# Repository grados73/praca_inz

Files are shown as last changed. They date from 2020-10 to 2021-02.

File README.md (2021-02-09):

# Praca Dyplomowa (inżynierska)
Tematem pracy była Analiza konstrukcyjna systemu śledzenia linii.
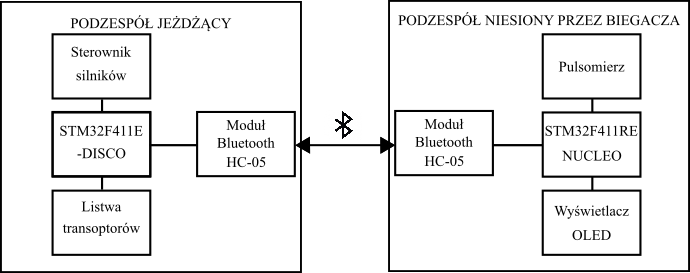
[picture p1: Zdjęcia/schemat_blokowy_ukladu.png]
Block diagram


Zaawansowane rozwiązania techniczne pomagają w osiąganiu coraz to lepszych wyników w różnych dyscyplinach sportowych,
towarzyszą podczas treningów zapewniając wsparcie i umożliwiając pokonywanie kolejnych granic oraz realizację założonych celów.
Wspierają one nie tylko zawodowych sportowców, ale również amatorów, ze względu na ich ogólną dostępność. 
Coraz częściej spotkać można bardzo zaawansowane aplikacje i urządzenia, wykorzystywane w sporcie, 
a oferta firm zajmujących się produkcją takiego sprzętu nieustannie się poszerza o nowe rozwiązania.

Celem pracy była realizacja robota, wykorzystującego system śledzenia linii, w celu utrzymywania zadanego tempa biegacza trenującego na bieżni lekkoatletycznej, 
aby osiągnąć większą efektywność treningów. Projekt składa się z dwóch podzespołów. 
Pierwszy z nich jest niesiony przez biegacza, jego zadaniem jest pomiar tętna i utrzymanie go w zakresie ustalonym przez ćwiczącego. 
Drugi moduł ma za zadanie jechać po ustalonej linii i utrzymywać zadane tempo.

https://youtu.be/Zt6rl9LgnUI

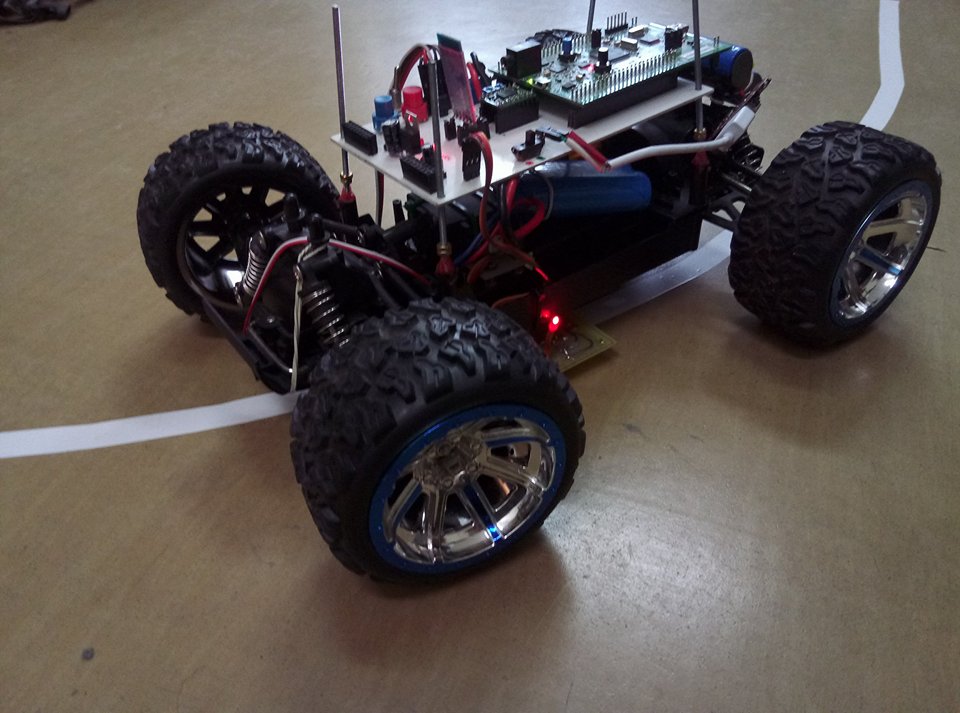
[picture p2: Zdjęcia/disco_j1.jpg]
Decio1

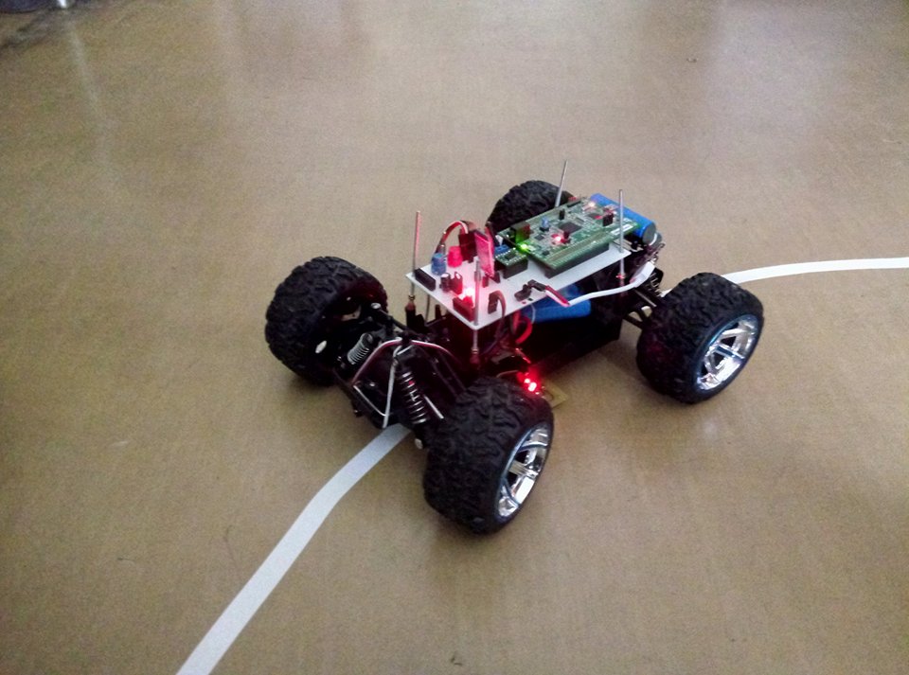
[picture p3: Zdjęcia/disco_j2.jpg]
Decio2

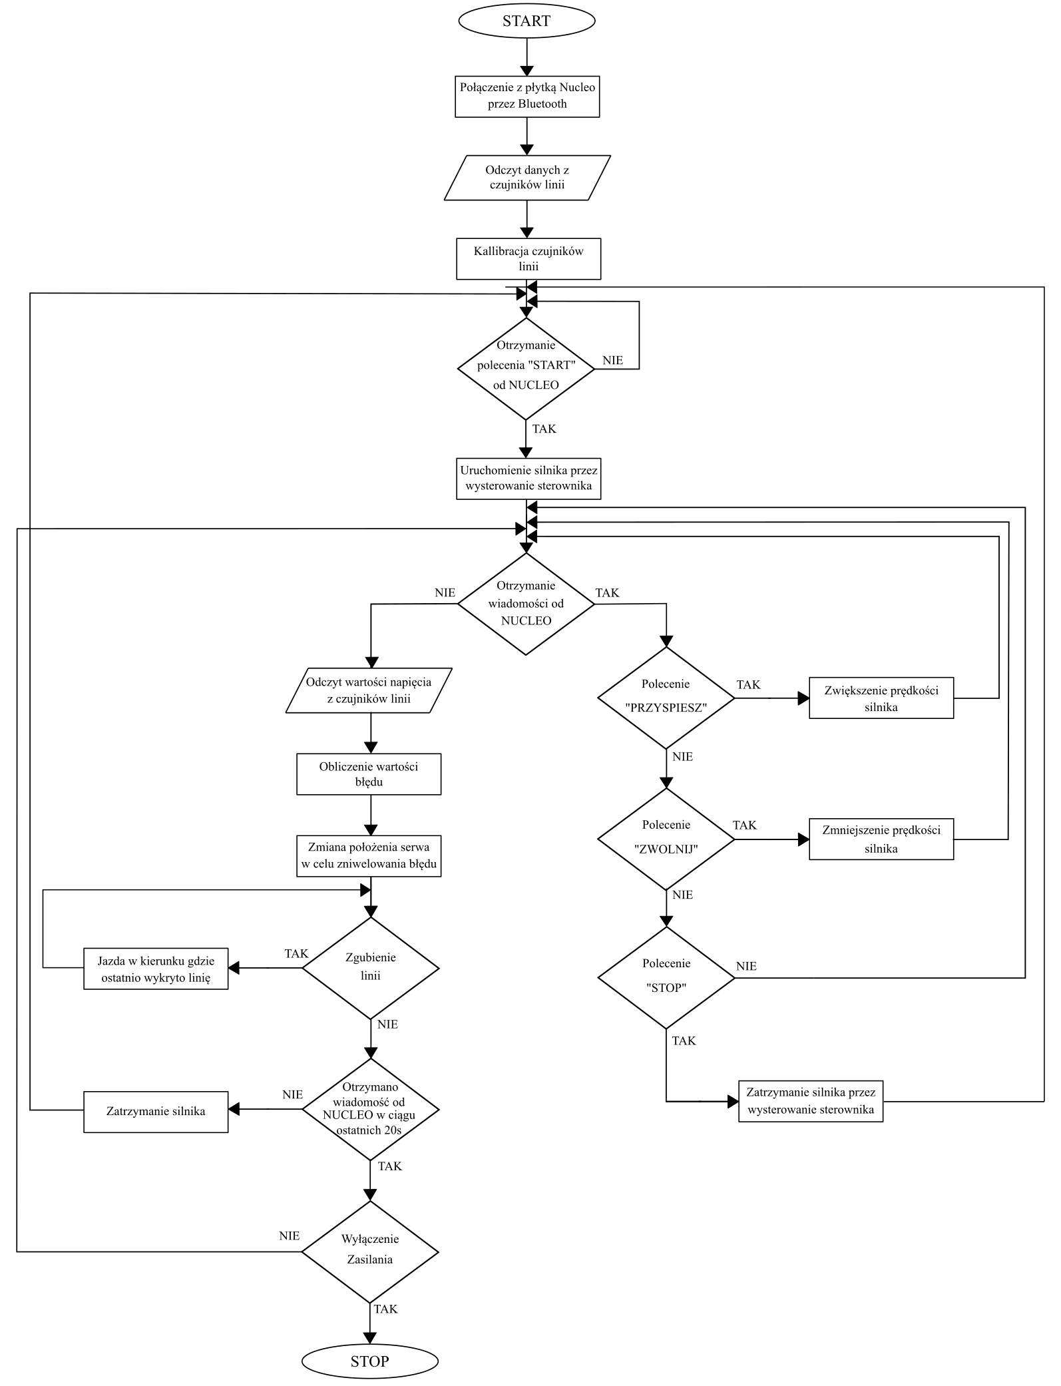
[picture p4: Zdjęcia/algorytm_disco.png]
ALGD1

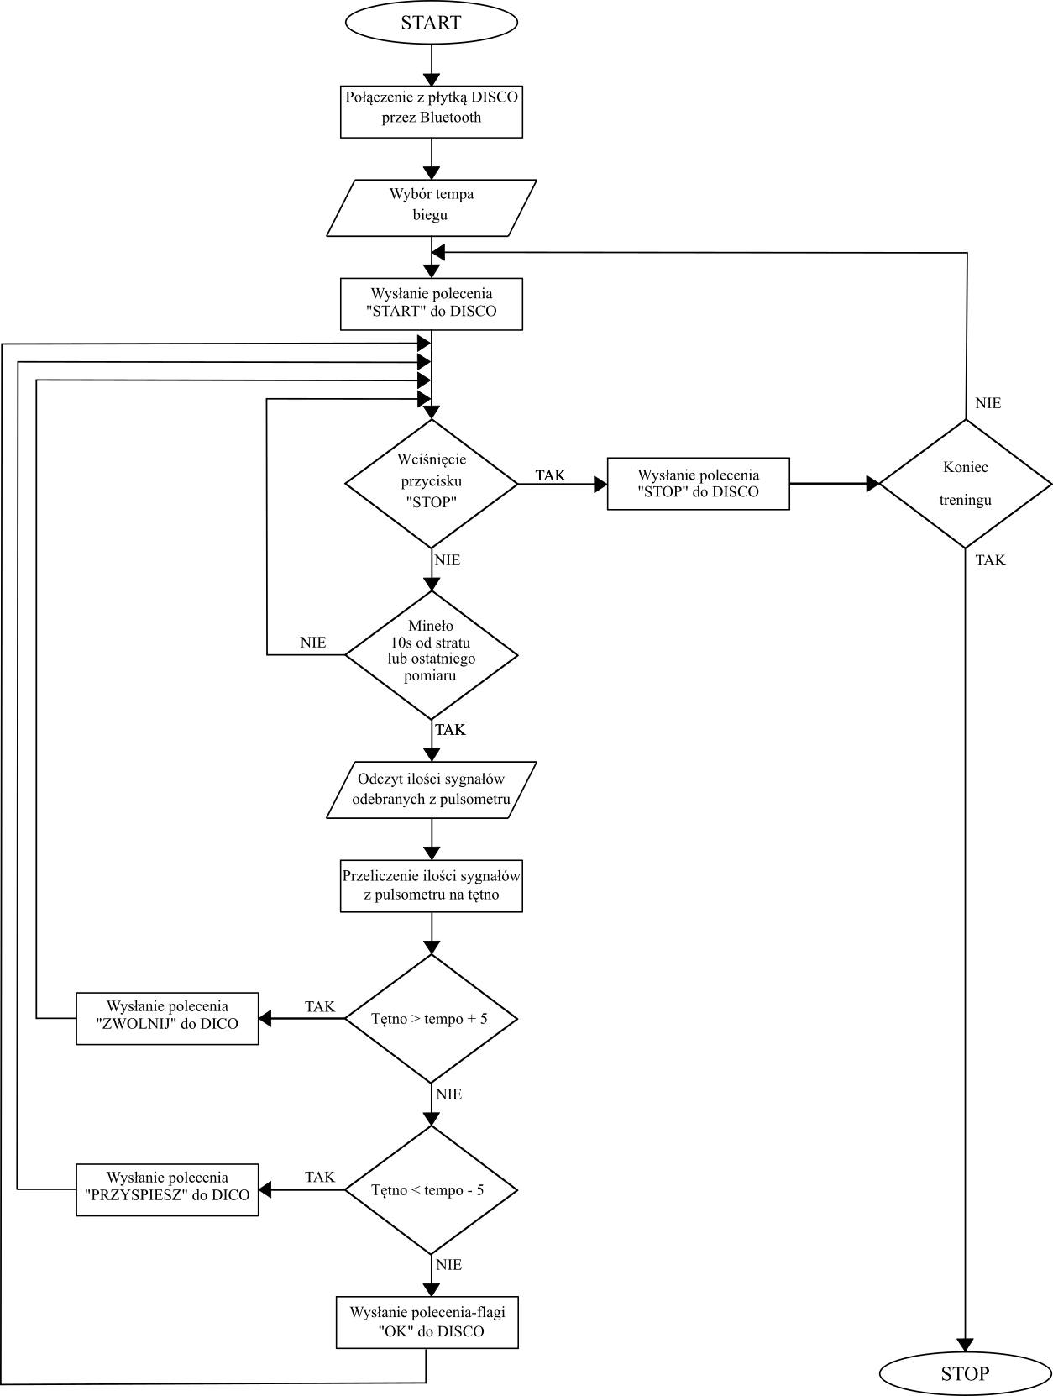
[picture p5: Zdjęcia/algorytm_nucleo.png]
ALGN1


Created by https://www.linkedin.com/in/kamil-gradowski-8706991aa - feel free to contact me! grados73

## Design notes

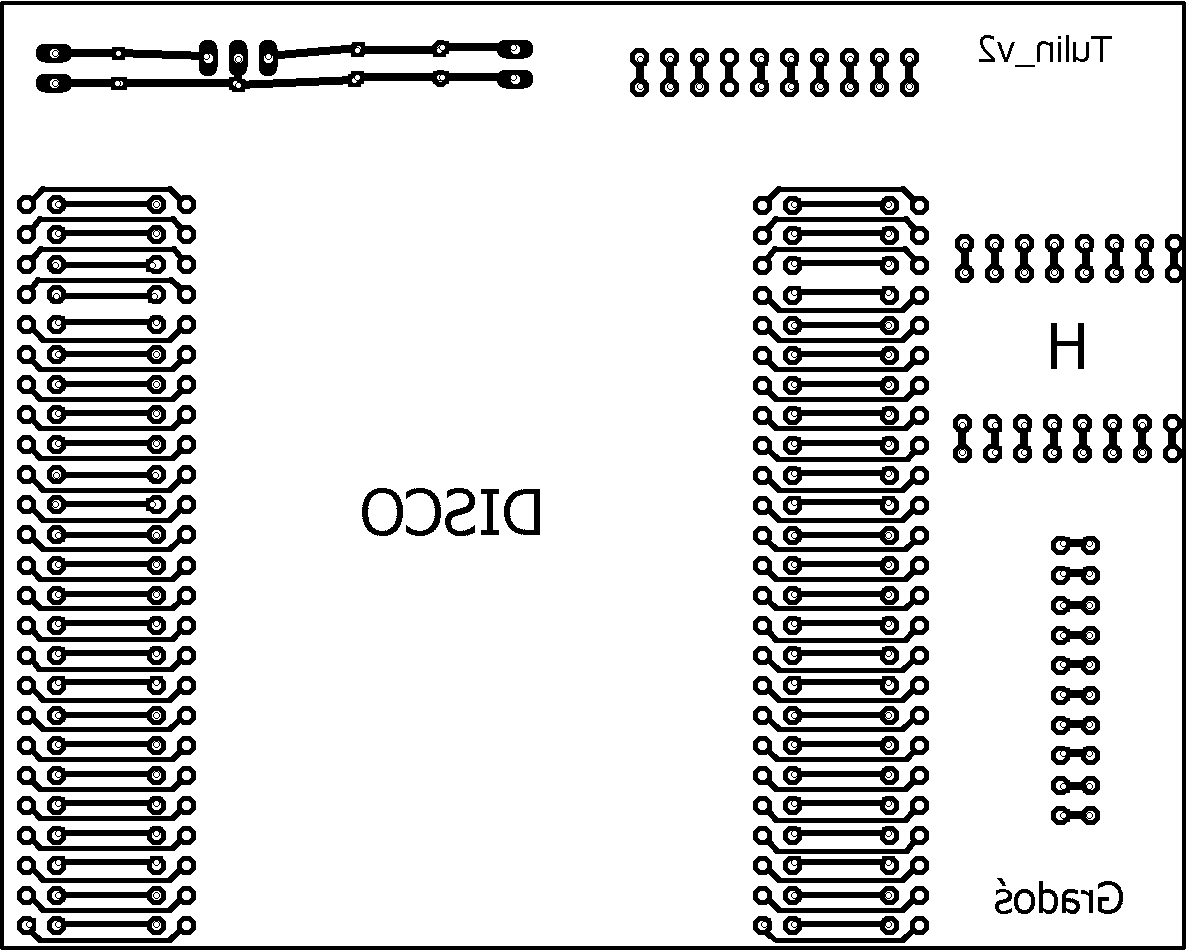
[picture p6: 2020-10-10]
eagle/Tulin_v.2_pr/Jedyna_prawdziwa.png

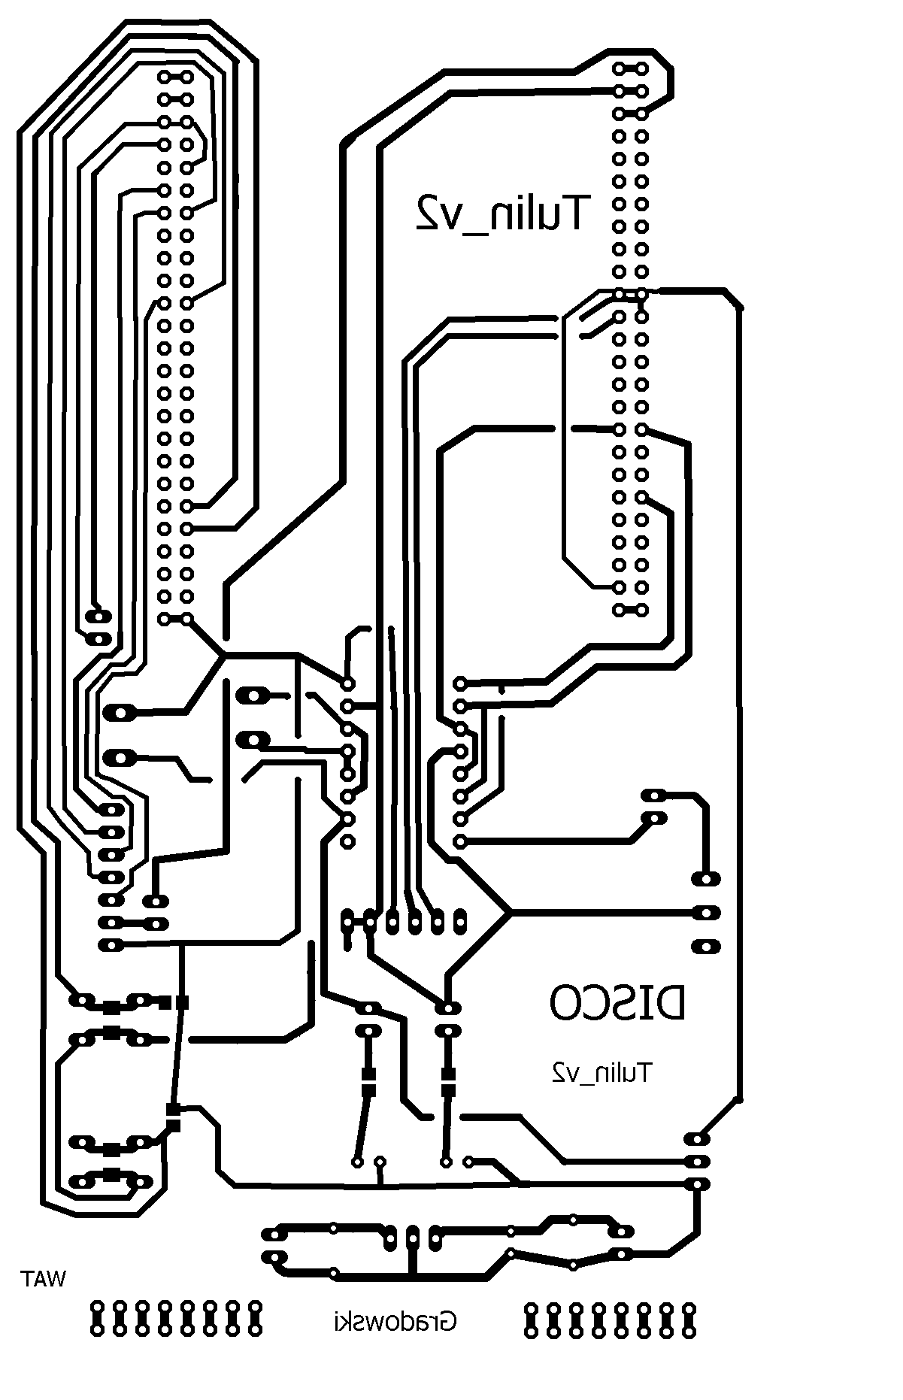
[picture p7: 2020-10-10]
eagle/TULIN_GOTOWE/Tulin_do_spr/got.png

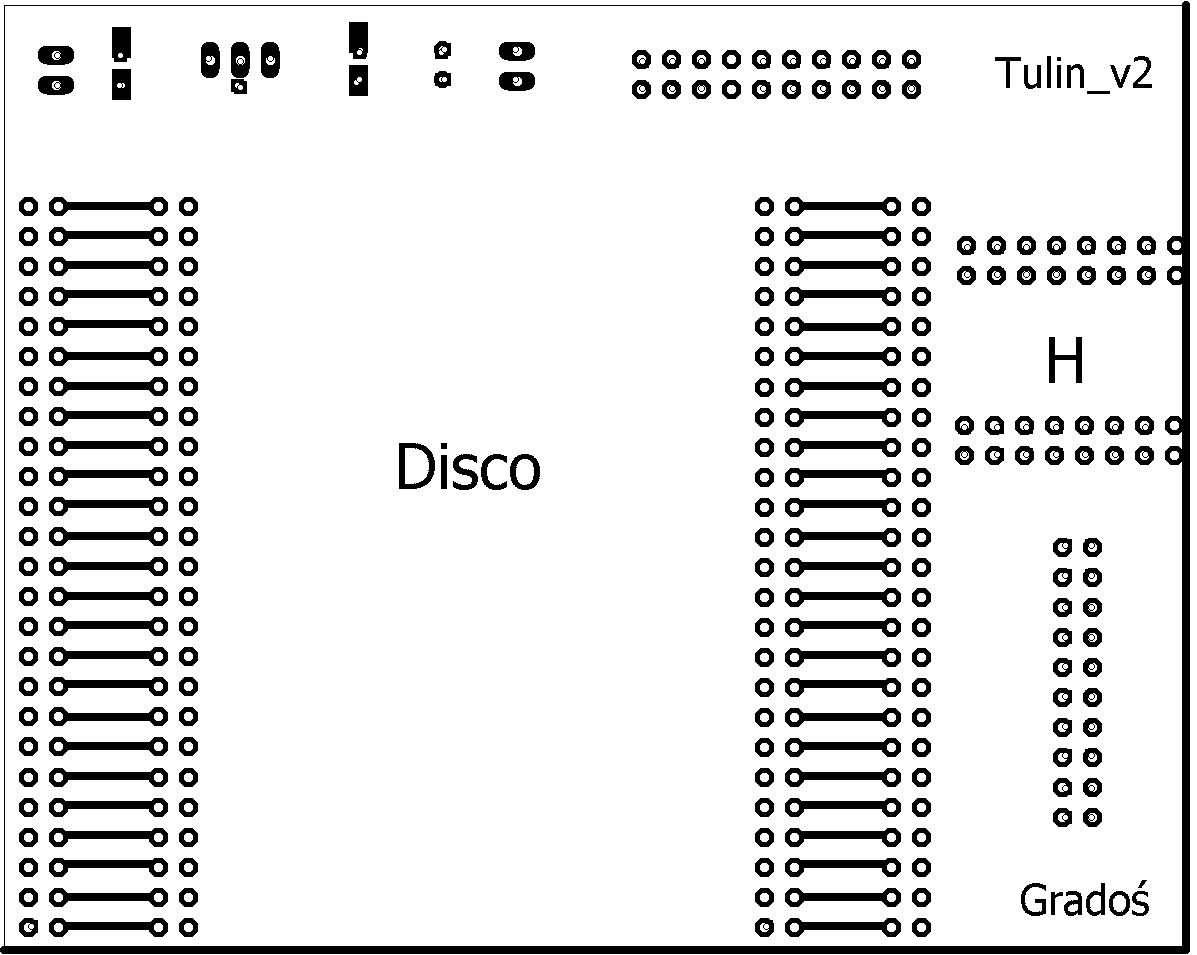
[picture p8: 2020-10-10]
eagle/Tulin_v.2_pr_czerwo/Top_strona2.png

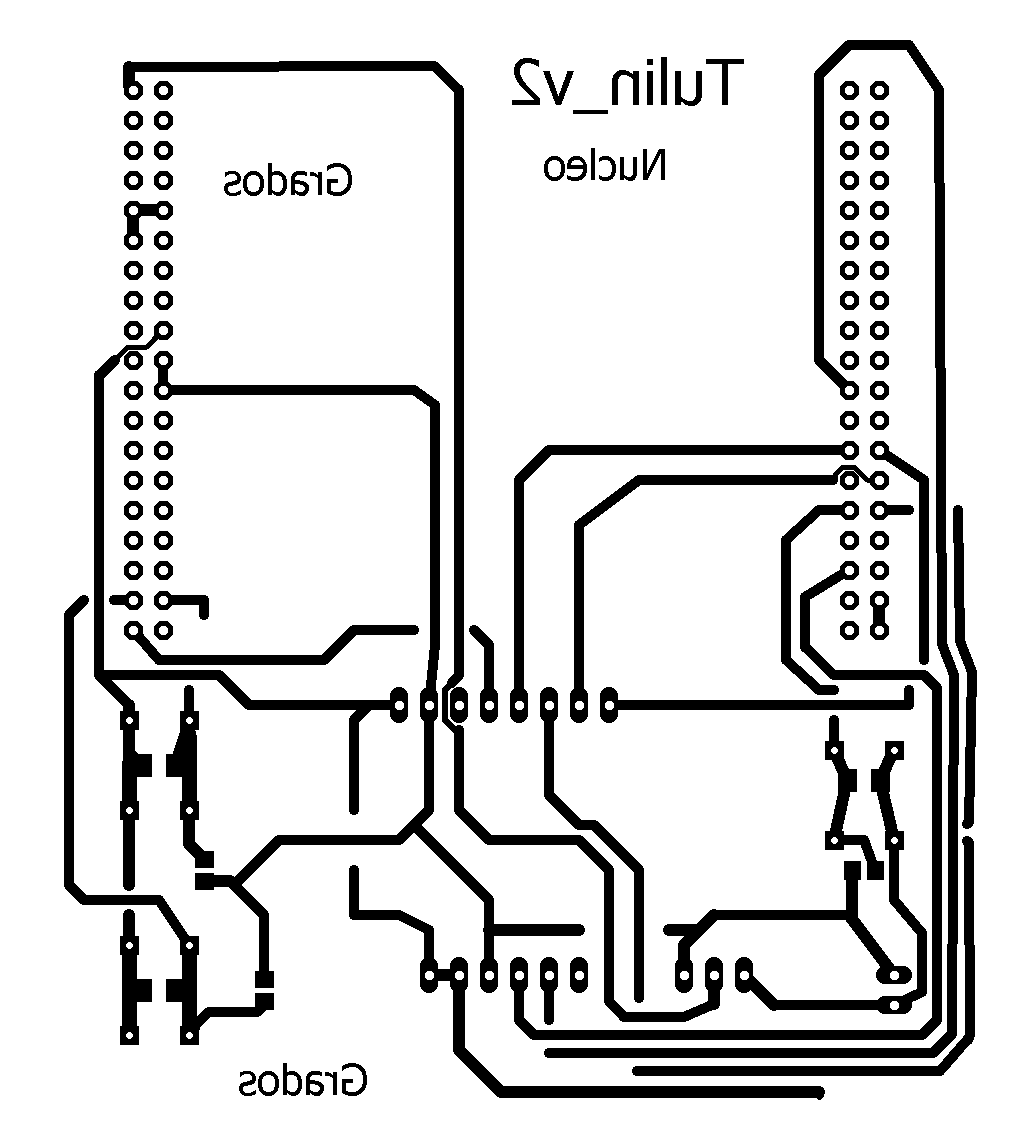
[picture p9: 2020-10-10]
Eagle_project/gotn.png

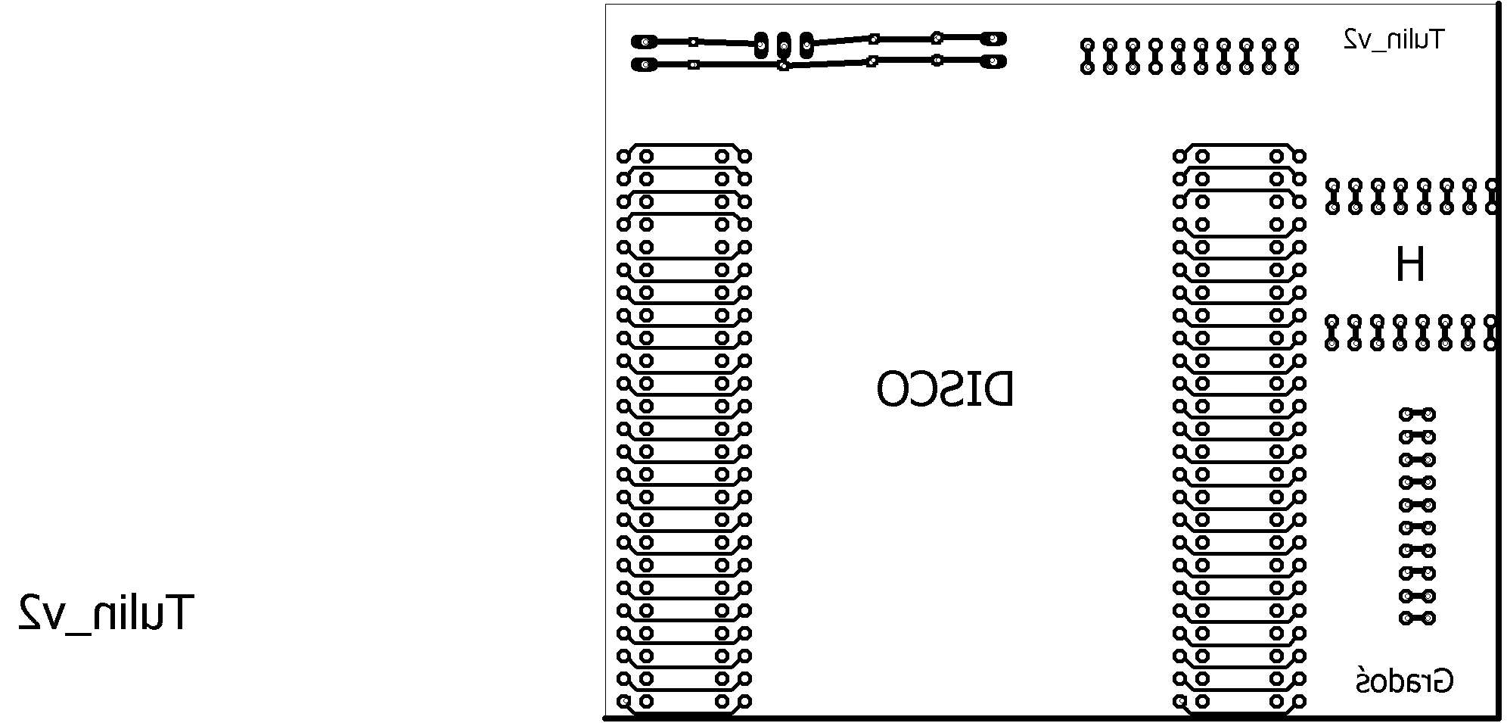
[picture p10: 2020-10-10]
eagle/Tulin_v.2_pr/butt_strona1.png

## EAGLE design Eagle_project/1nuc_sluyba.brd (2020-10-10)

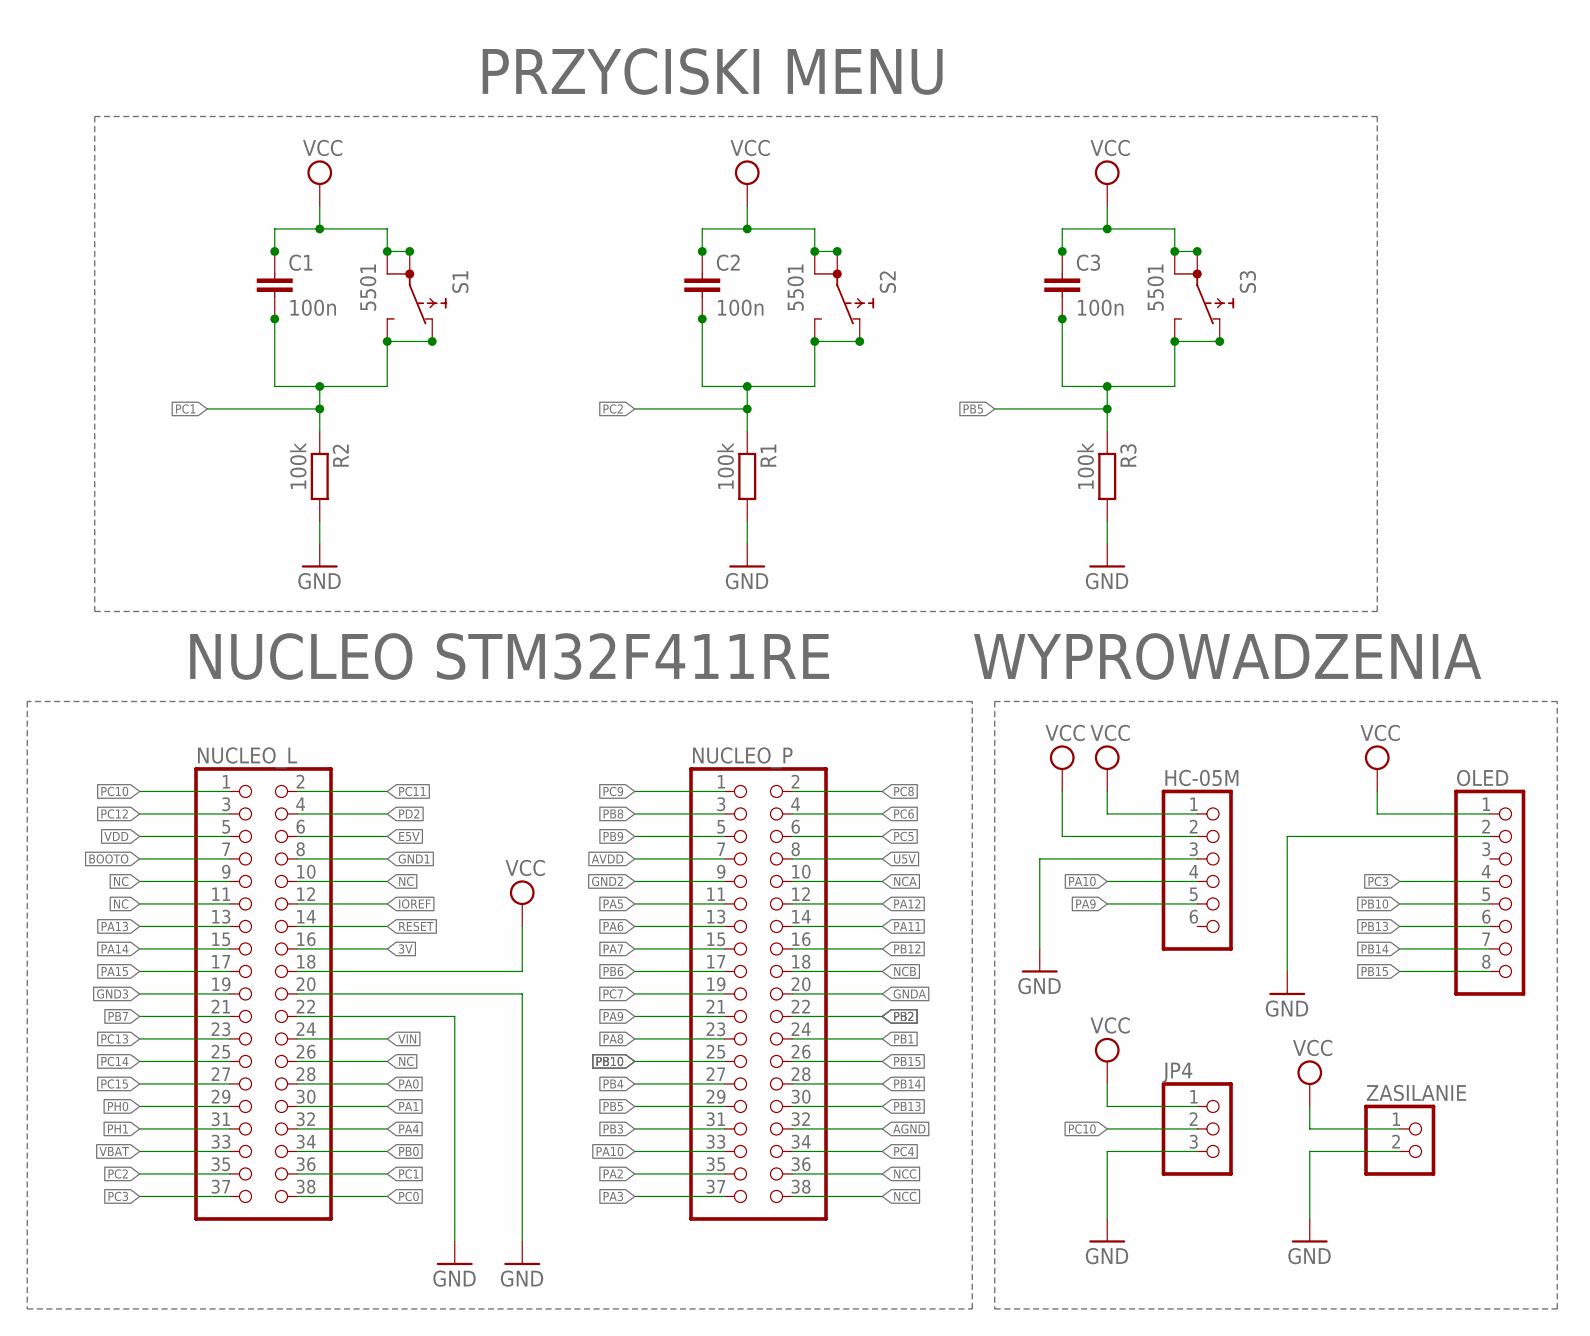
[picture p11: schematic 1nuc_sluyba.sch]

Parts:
C1, C2, C3: 100n; C1206
HC-05M: PINHD-1X6; 1X06
JP4: PINHD-1X3; 1X03
NUCLEO_L: PINHD-2X19; 2X19
NUCLEO_P: PINHD-2X19; 2X19
OLED: PINHD-1X8; 1X08
R1, R2, R3: 100k; R0805
S1, S2, S3: 5501
ZASILANIE: PINHD-1X2; 1X02

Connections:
3V: NUCLEO_L.16
AGND: NUCLEO_P.32
AVDD: NUCLEO_P.7
BOOTO: NUCLEO_L.7
E5V: NUCLEO_L.6
GND: HC-05M.3, JP4.3, NUCLEO_L.20, NUCLEO_L.22, OLED.2, R1.2, R2.2, R3.2, ZASILANIE.2; also elsewhere on the board
GND1: NUCLEO_L.8
GND2: NUCLEO_P.9
GND3: NUCLEO_L.19
GNDA: NUCLEO_P.20
IOREF: NUCLEO_L.12
NC: NUCLEO_L.9, NUCLEO_L.10, NUCLEO_L.11, NUCLEO_L.26
NCA: NUCLEO_P.10
NCB: NUCLEO_P.18
NCC: NUCLEO_P.36, NUCLEO_P.38
PA0: NUCLEO_L.28
PA1: NUCLEO_L.30
PA2: NUCLEO_P.35
PA3: NUCLEO_P.37
PA4: NUCLEO_L.32
PA5: NUCLEO_P.11
PA6: NUCLEO_P.13
PA7: NUCLEO_P.15
PA8: NUCLEO_P.23
PA9: HC-05M.5, NUCLEO_P.21
PA10: HC-05M.4, NUCLEO_P.33
PA11: NUCLEO_P.14
PA12: NUCLEO_P.12
PA13: NUCLEO_L.13
PA14: NUCLEO_L.15
PA15: NUCLEO_L.17
PB0: NUCLEO_L.34
PB1: NUCLEO_P.24
PB2: NUCLEO_P.22
PB3: NUCLEO_P.31
PB4: NUCLEO_P.27
PB5: C3.2, NUCLEO_P.29, R3.1, S3.NC, S3.NO
PB6: NUCLEO_P.17
PB7: NUCLEO_L.21
PB8: NUCLEO_P.3
PB9: NUCLEO_P.5
PB10: NUCLEO_P.25, OLED.5
PB12: NUCLEO_P.16
PB13: NUCLEO_P.30, OLED.6
PB14: NUCLEO_P.28, OLED.7
PB15: NUCLEO_P.26, OLED.8
PC0: NUCLEO_L.38
PC1: C1.2, NUCLEO_L.36, R2.1, S1.NC, S1.NO
PC2: C2.2, NUCLEO_L.35, R1.1, S2.NC, S2.NO
PC3: NUCLEO_L.37, OLED.4
PC4: NUCLEO_P.34
PC5: NUCLEO_P.6
PC6: NUCLEO_P.4
PC7: NUCLEO_P.19
PC8: NUCLEO_P.2
PC9: NUCLEO_P.1
PC10: JP4.2, NUCLEO_L.1; also elsewhere on the board
PC11: NUCLEO_L.2
PC12: NUCLEO_L.3
PC13: NUCLEO_L.23
PC14: NUCLEO_L.25
PC15: NUCLEO_L.27
PD2: NUCLEO_L.4
PH0: NUCLEO_L.29
PH1: NUCLEO_L.31
RESET: NUCLEO_L.14
U5V: NUCLEO_P.8
VBAT: NUCLEO_L.33
VCC: C1.1, C2.1, C3.1, HC-05M.1, HC-05M.2, JP4.1, NUCLEO_L.18, OLED.1, S1.1A, S1.1B, S2.1A, S2.1B, S3.1A, S3.1B, ZASILANIE.1; also elsewhere on the board
VDD: NUCLEO_L.5
VIN: NUCLEO_L.24

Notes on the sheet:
NUCLEO STM32F411RE
WYPROWADZENIA
PRZYCISKI MENU

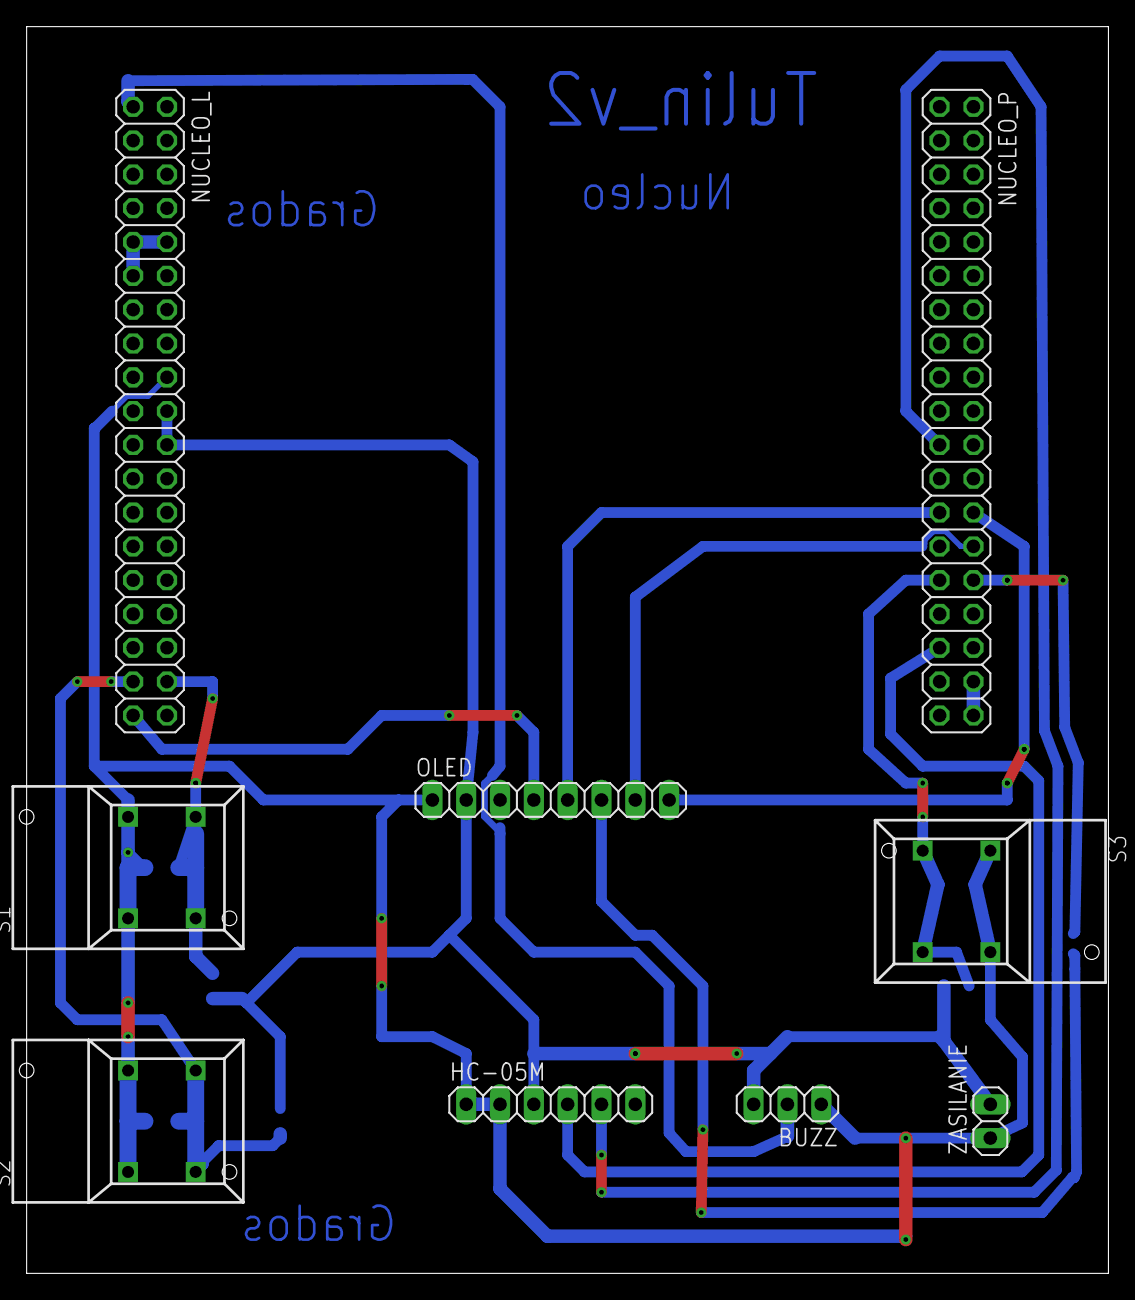
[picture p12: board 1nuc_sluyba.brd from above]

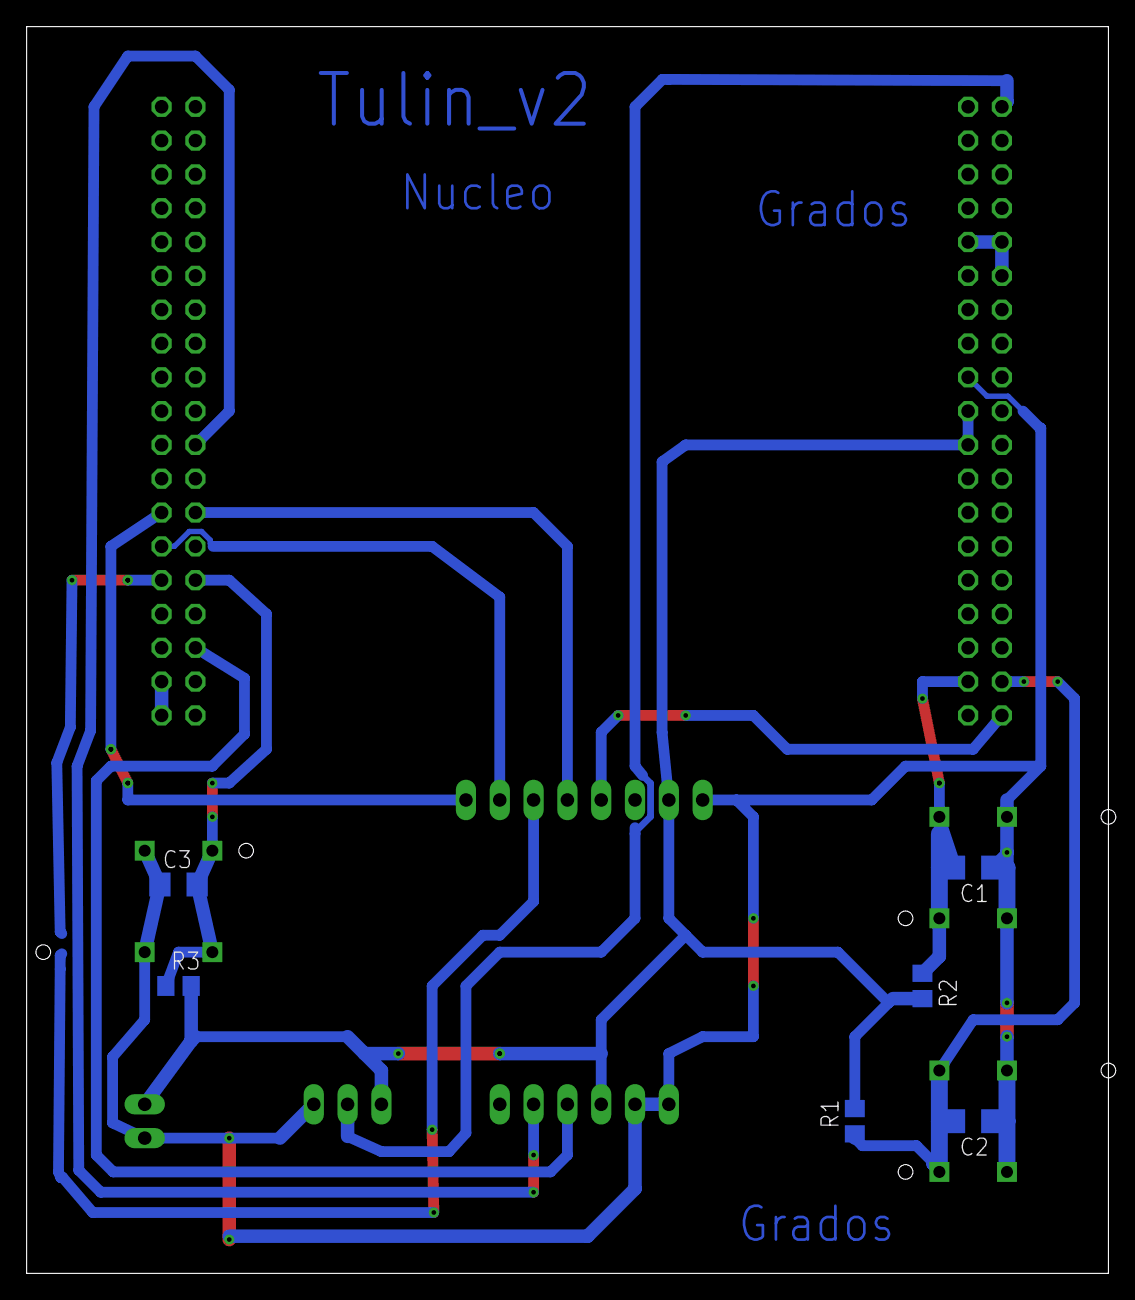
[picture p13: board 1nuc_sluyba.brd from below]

Board: 2 copper layers, 81.3 x 93.7 mm, 15 parts (6 on the bottom side), 15 nets.

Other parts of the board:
BUZZ: 1X03

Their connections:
GND: BUZZ.3; also elsewhere on the board
PC10: BUZZ.2; also elsewhere on the board
VCC: BUZZ.1; also elsewhere on the board

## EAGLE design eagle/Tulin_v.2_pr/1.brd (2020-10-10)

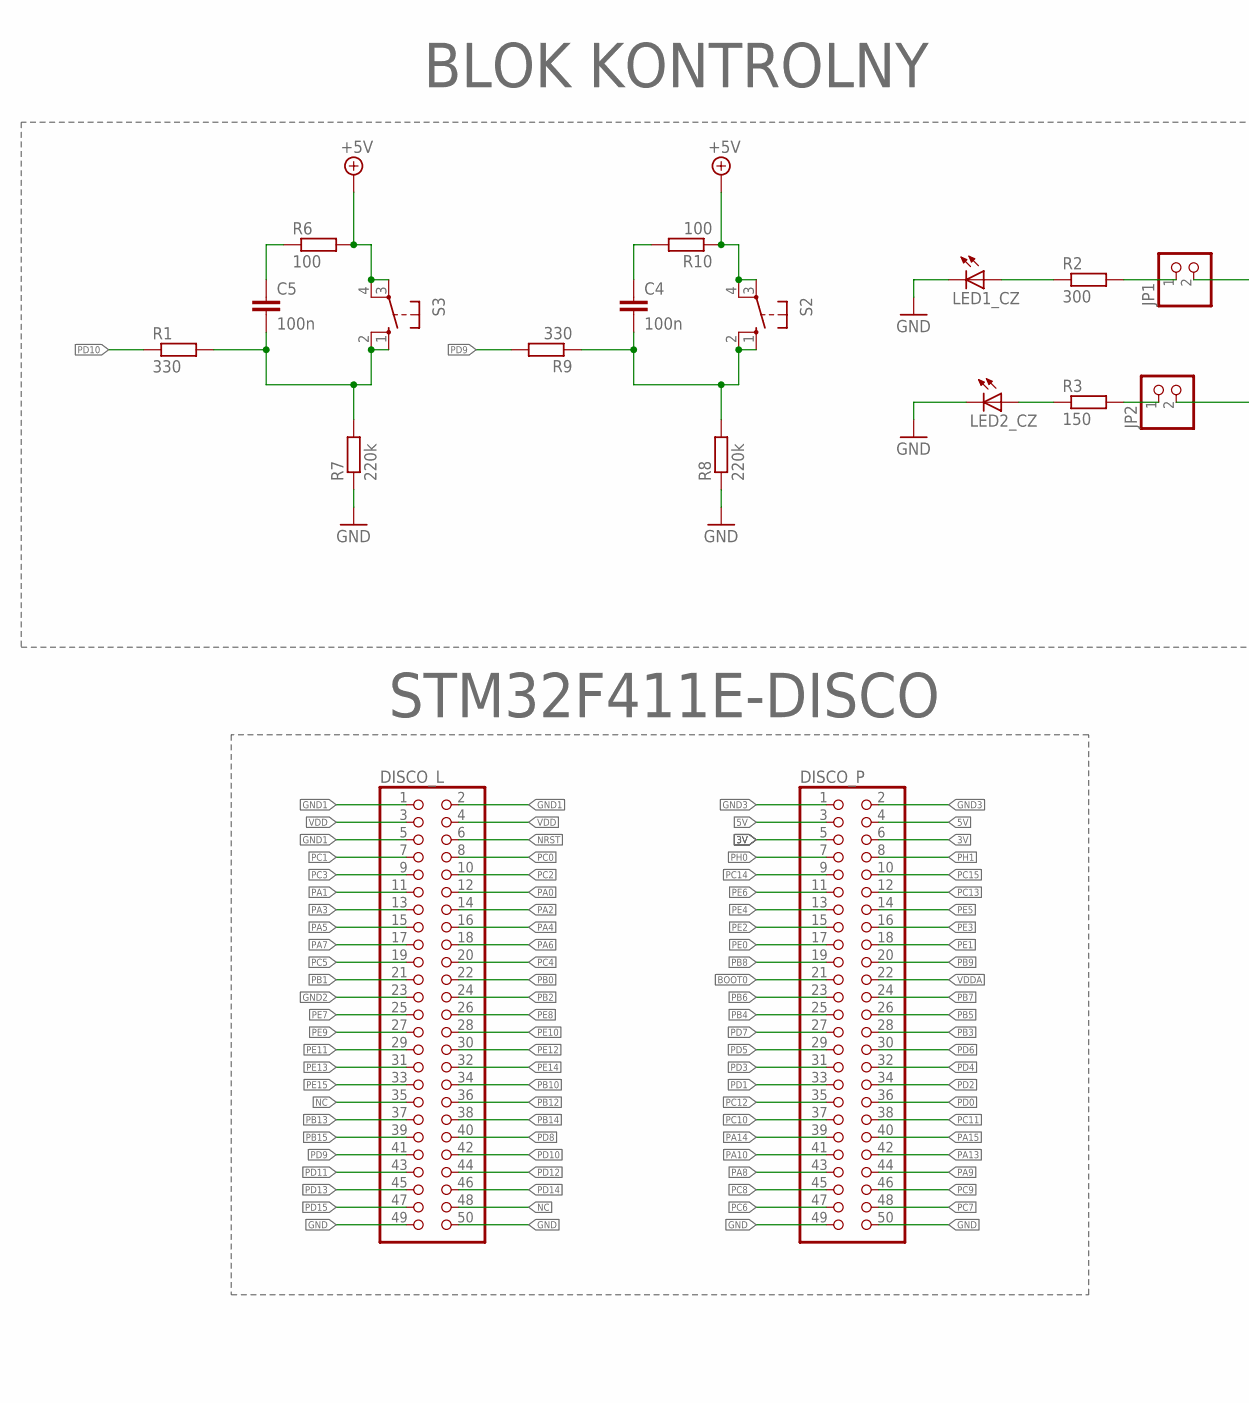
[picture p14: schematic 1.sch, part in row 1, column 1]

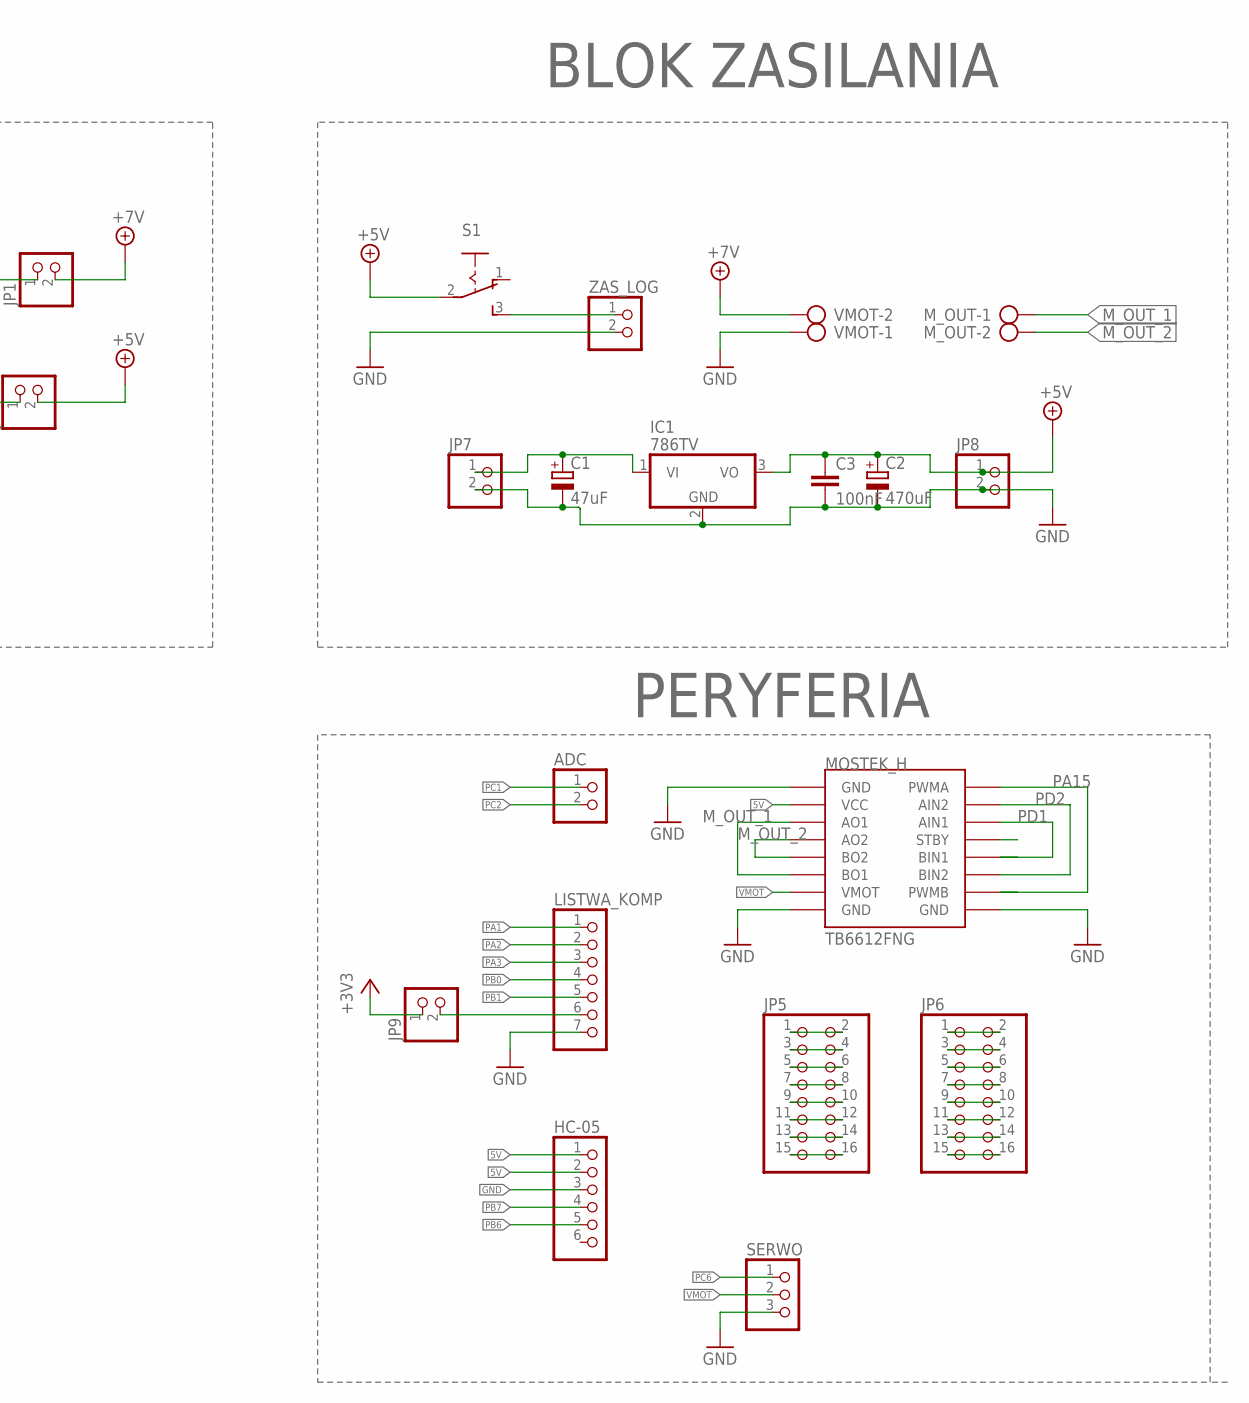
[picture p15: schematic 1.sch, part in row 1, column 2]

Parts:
ADC: PINHD-1X2; 1X02
C1: 47uF; 153CLV-0405
C2: 470uF; 153CLV-0405
C3: 100nF; C025-024X044
C4, C5: 100n; C1206
DISCO_L: PINHD-2X25; 2X25
DISCO_P: PINHD-2X25; 2X25
HC-05: PINHD-1X6; 1X06
IC1: 786TV; TO220V
JP1, JP2, JP7, JP8, JP9: PINHD-1X2; 1X02
JP5, JP6: PINHD-2X8; 2X08
LED1_CZ, LED2_CZ: LEDSML1206; SML1206
LISTWA_KOMP: PINHD-1X7; 1X07
MOSTEK_H: MODUL_POLOLU
M_OUT: AK300/2
R1, R9: 330; R0805
R2: 300; R0805
R3: 150; R0805
R6, R10: 100; R0805
R7, R8: 220k; R0805
S1: 255SB
S2, S3: 10-XX; B3F-10XX
SERWO: PINHD-1X3; 1X03
VMOT: AK300/2
ZAS_LOG: PINHD-1X2/90; 1X02/90

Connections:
3V: DISCO_P.5, DISCO_P.6, JP9.1
5V: C2.+, C3.1, DISCO_P.3, DISCO_P.4, HC-05.1, HC-05.2, IC1.3 (VO), JP2.2, JP8.1, MOSTEK_H.VCC, R6.2, R10.1, S1.2, S2.3, S2.4 (P1), S3.3, S3.4 (P1)
A: JP9.2, LISTWA_KOMP.6
BOOT0: DISCO_P.21
GND: C1.-, C2.-, C3.2, DISCO_L.49, DISCO_L.50, DISCO_P.49, DISCO_P.50, HC-05.3, IC1.2 (GND), JP7.2, JP8.2, LED1_CZ.C, LED2_CZ.C, LISTWA_KOMP.7, MOSTEK_H.GND1 (GND), MOSTEK_H.GND2 (GND), MOSTEK_H.GND3 (GND), R7.1, R8.1, SERWO.3, VMOT.1, ZAS_LOG.2
GND1: DISCO_L.1, DISCO_L.2, DISCO_L.5
GND2: DISCO_L.23
GND3: DISCO_P.1, DISCO_P.2
M_OUT_1: MOSTEK_H.AO1, MOSTEK_H.BO1, M_OUT.1
M_OUT_2: MOSTEK_H.A02 (AO2), MOSTEK_H.BO2, M_OUT.2
unnamed: JP5.1, JP5.2
unnamed: JP5.3, JP5.4
unnamed: JP5.5, JP5.6
unnamed: JP5.7, JP5.8
unnamed: JP5.9, JP5.10
unnamed: JP5.11, JP5.12
unnamed: JP5.13, JP5.14
unnamed: JP5.15, JP5.16
unnamed: JP6.1, JP6.2
unnamed: JP6.3, JP6.4
unnamed: JP6.5, JP6.6
unnamed: JP6.7, JP6.8
unnamed: JP6.9, JP6.10
unnamed: JP6.11, JP6.12
unnamed: JP6.13, JP6.14
unnamed: JP6.15, JP6.16
unnamed: C1.+, IC1.1 (VI), JP7.1
unnamed: S1.3 (S), ZAS_LOG.1
unnamed: LED1_CZ.A, R2.1
unnamed: LED2_CZ.A, R3.1
unnamed: C4.2, R8.2, R9.1, S2.1 (S), S2.2 (S1)
unnamed: JP1.1, R2.2
unnamed: C5.2, R1.2, R7.2, S3.1 (S), S3.2 (S1)
unnamed: JP2.1, R3.2
unnamed: C4.1, R10.2
unnamed: C5.1, R6.1
NC: DISCO_L.35, DISCO_L.48
NRST: DISCO_L.6
PA0: DISCO_L.12
PA1: DISCO_L.11, LISTWA_KOMP.1
PA2: DISCO_L.14, LISTWA_KOMP.2
PA3: DISCO_L.13, LISTWA_KOMP.3
PA4: DISCO_L.16
PA5: DISCO_L.15
PA6: DISCO_L.18
PA7: DISCO_L.17
PA8: DISCO_P.43
PA9: DISCO_P.44
PA10: DISCO_P.41
PA13: DISCO_P.42
PA14: DISCO_P.39
PA15: DISCO_P.40, MOSTEK_H.PWMA, MOSTEK_H.PWMB
PB0: DISCO_L.22, LISTWA_KOMP.4
PB1: DISCO_L.21, LISTWA_KOMP.5
PB2: DISCO_L.24
PB3: DISCO_P.28
PB4: DISCO_P.25
PB5: DISCO_P.26
PB6: DISCO_P.23, HC-05.5
PB7: DISCO_P.24, HC-05.4
PB8: DISCO_P.19
PB9: DISCO_P.20
PB10: DISCO_L.34
PB12: DISCO_L.36
PB13: DISCO_L.37
PB14: DISCO_L.38
PB15: DISCO_L.39
PC0: DISCO_L.8
PC1: ADC.1, DISCO_L.7
PC2: ADC.2, DISCO_L.10
PC3: DISCO_L.9
PC4: DISCO_L.20
PC5: DISCO_L.19
PC6: DISCO_P.47, SERWO.1
PC7: DISCO_P.48
PC8: DISCO_P.45
PC9: DISCO_P.46
PC10: DISCO_P.37
PC11: DISCO_P.38
PC12: DISCO_P.35
PC13: DISCO_P.12
PC14: DISCO_P.9
PC15: DISCO_P.10
PD0: DISCO_P.36
PD1: DISCO_P.33, MOSTEK_H.AIN1, MOSTEK_H.BIN1
PD2: DISCO_P.34, MOSTEK_H.AIN2, MOSTEK_H.BIN2
PD3: DISCO_P.31
PD4: DISCO_P.32
PD5: DISCO_P.29
PD6: DISCO_P.30
PD7: DISCO_P.27
PD8: DISCO_L.40
PD9: DISCO_L.41, R9.2
PD10: DISCO_L.42, R1.1
PD11: DISCO_L.43
PD12: DISCO_L.44
PD13: DISCO_L.45
PD14: DISCO_L.46
PD15: DISCO_L.47
PE0: DISCO_P.17
PE1: DISCO_P.18
PE2: DISCO_P.15
PE3: DISCO_P.16
PE4: DISCO_P.13
PE5: DISCO_P.14
PE6: DISCO_P.11
PE7: DISCO_L.25
PE8: DISCO_L.26
PE9: DISCO_L.27
PE10: DISCO_L.28
PE11: DISCO_L.29
PE12: DISCO_L.30
PE13: DISCO_L.31
PE14: DISCO_L.32
PE15: DISCO_L.33
PH0: DISCO_P.7
PH1: DISCO_P.8
VDD: DISCO_L.3, DISCO_L.4
VDDA: DISCO_P.22
VMOT: JP1.2, MOSTEK_H.VMOT, SERWO.2, VMOT.2

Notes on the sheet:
BLOK ZASILANIA
BLOK KONTROLNY
STM32F411E-DISCO
PERYFERIA

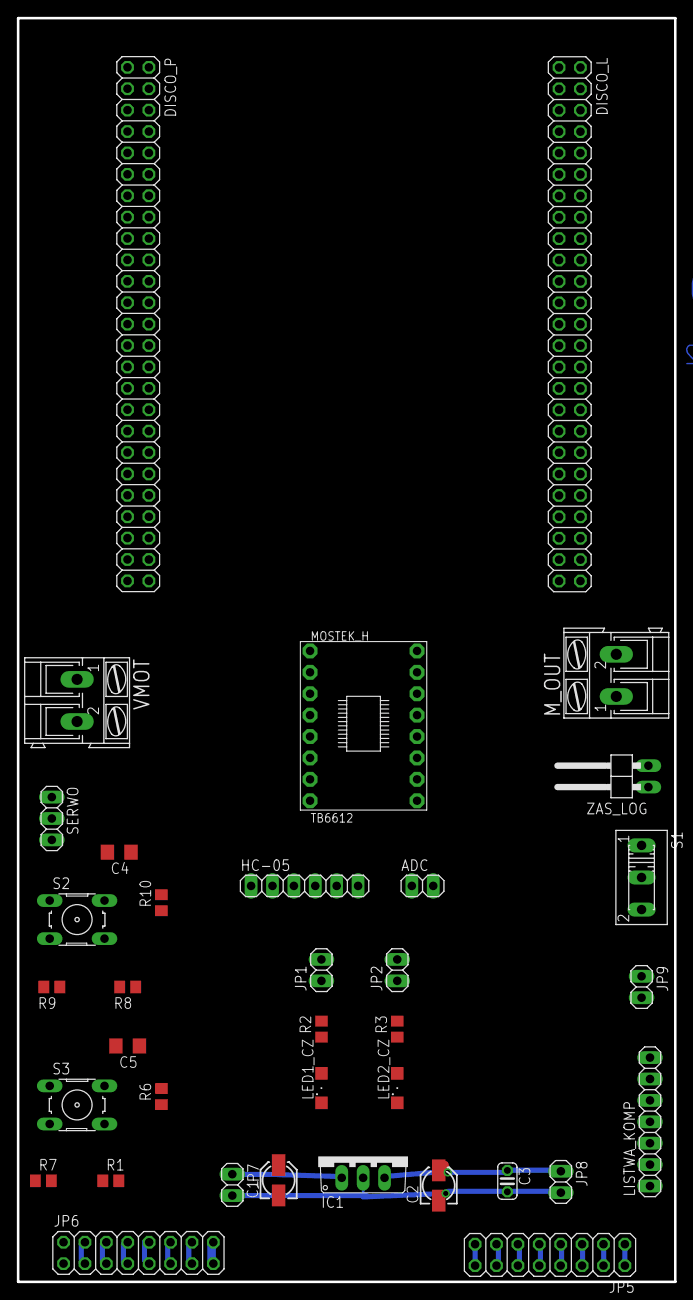
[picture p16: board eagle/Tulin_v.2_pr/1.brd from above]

Board: 2 copper layers, 78.0 x 150.0 mm, 36 parts (0 on the bottom side), 52 nets.

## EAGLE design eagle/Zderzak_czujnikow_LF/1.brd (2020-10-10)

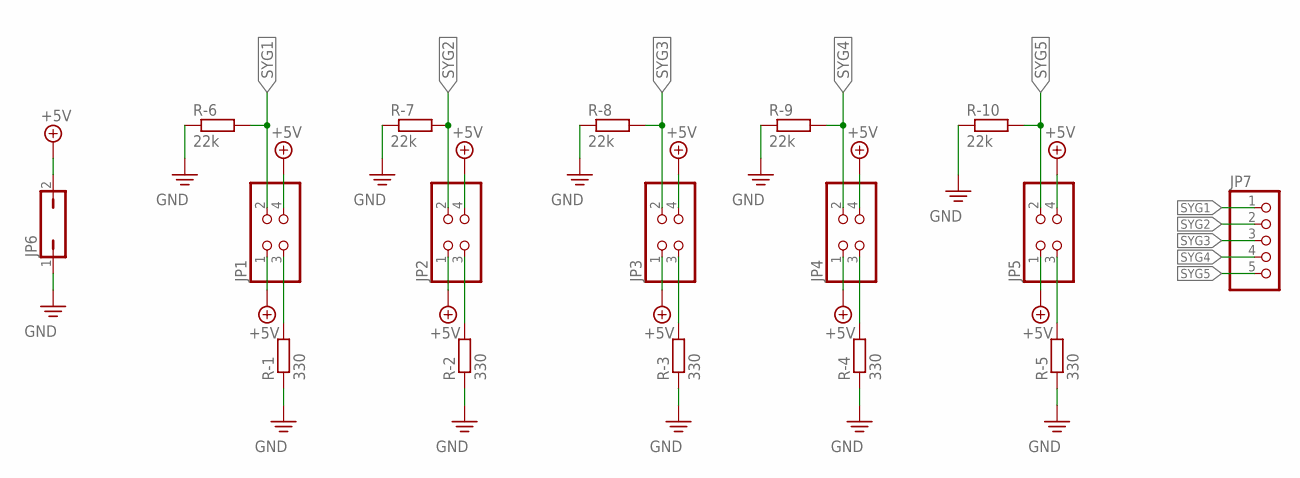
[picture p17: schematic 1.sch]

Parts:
JP1, JP2, JP3, JP4, JP5: PINHD-2X2; 2X02
JP6: JP1Q; JP1
JP7: PINHD-1X5; 1X05
R-1, R-2, R-3, R-4, R-5: 330; 0204/7
R-6, R-7, R-8, R-9, R-10: 22k; 0204/7

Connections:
+5V: JP1.1, JP1.4, JP2.1, JP2.4, JP3.1, JP3.4, JP4.1, JP4.4, JP5.1, JP5.4, JP6.2
unnamed: JP1.3, R-1.2
unnamed: JP2.3, R-2.2
unnamed: JP3.3, R-3.2
unnamed: JP4.3, R-4.2
unnamed: JP5.3, R-5.2
PE: JP6.1, R-1.1, R-2.1, R-3.1, R-4.1, R-5.1, R-6.1, R-7.1, R-8.1, R-9.1, R-10.1
SYG1: JP1.2, JP7.1, R-6.2
SYG2: JP2.2, JP7.2, R-7.2
SYG3: JP3.2, JP7.3, R-8.2
SYG4: JP4.2, JP7.4, R-9.2
SYG5: JP5.2, JP7.5, R-10.2

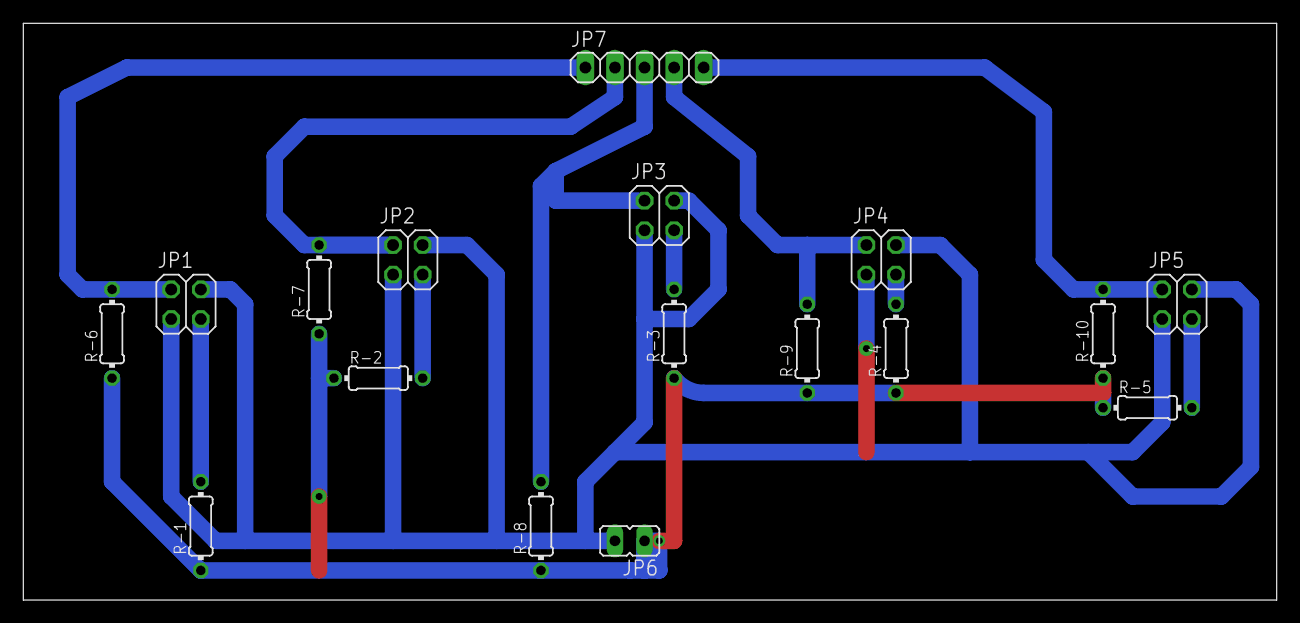
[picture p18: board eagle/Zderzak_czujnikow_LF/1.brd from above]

Board: 2 copper layers, 107.6 x 49.5 mm, 17 parts (0 on the bottom side), 12 nets.

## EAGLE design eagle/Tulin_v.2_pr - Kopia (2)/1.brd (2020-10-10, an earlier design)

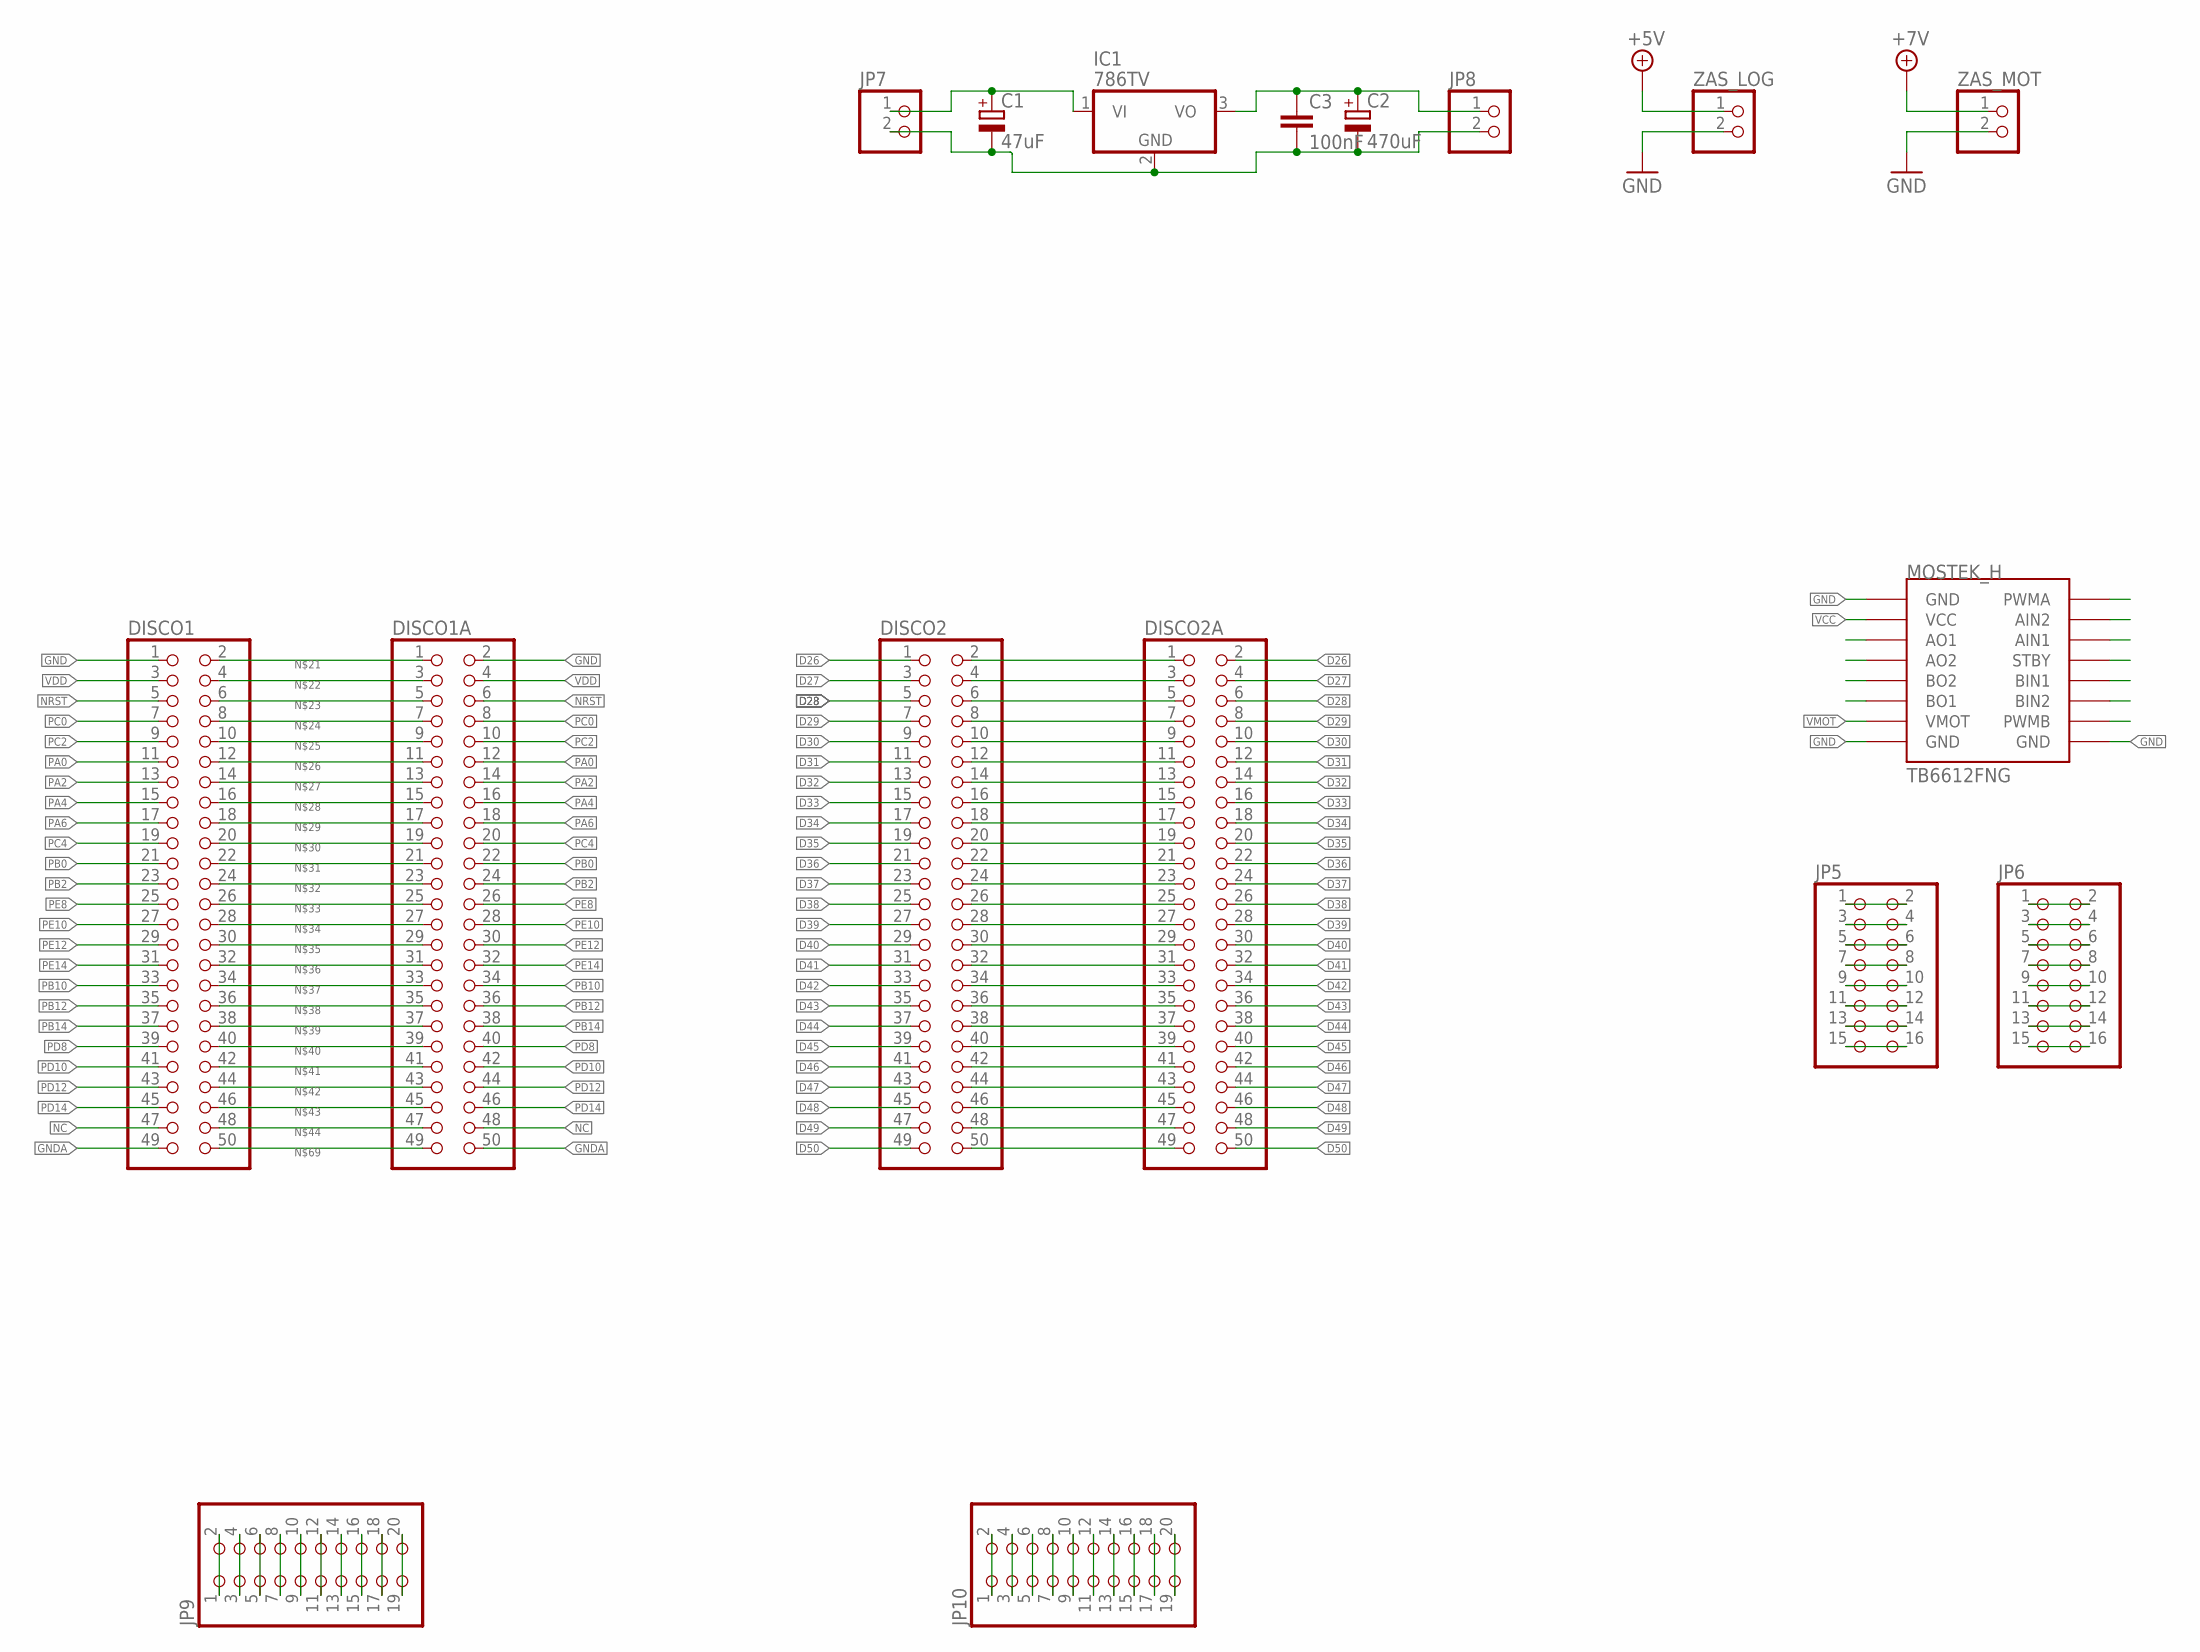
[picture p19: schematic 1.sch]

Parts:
C1: 47uF; 153CLV-0405
C2: 470uF; 153CLV-0405
C3: 100nF; C025-024X044
DISCO1, DISCO1A, DISCO2, DISCO2A: PINHD-2X25; 2X25
IC1: 786TV; TO220V
JP5, JP6: PINHD-2X8; 2X08
JP7, JP8: PINHD-1X2; 1X02
JP9, JP10: PINHD-2X10; 2X10
MOSTEK_H: MODUL_POLOLU
ZAS_LOG: PINHD-1X2/90; 1X02/90
ZAS_MOT: PINHD-1X2/90; 1X02/90

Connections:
+5V: ZAS_LOG.1
D26: DISCO2.1, DISCO2A.2
D27: DISCO2.3, DISCO2A.4
D28: DISCO2.5, DISCO2A.6
D29: DISCO2.7, DISCO2A.8
D30: DISCO2.9, DISCO2A.10
D31: DISCO2.11, DISCO2A.12
D32: DISCO2.13, DISCO2A.14
D33: DISCO2.15, DISCO2A.16
D34: DISCO2.17, DISCO2A.18
D35: DISCO2.19, DISCO2A.20
D36: DISCO2.21, DISCO2A.22
D37: DISCO2.23, DISCO2A.24
D38: DISCO2.25, DISCO2A.26
D39: DISCO2.27, DISCO2A.28
D40: DISCO2.29, DISCO2A.30
D41: DISCO2.31, DISCO2A.32
D42: DISCO2.33, DISCO2A.34
D43: DISCO2.35, DISCO2A.36
D44: DISCO2.37, DISCO2A.38
D45: DISCO2.39, DISCO2A.40
D46: DISCO2.41, DISCO2A.42
D47: DISCO2.43, DISCO2A.44
D48: DISCO2.45, DISCO2A.46
D49: DISCO2.47, DISCO2A.48
D50: DISCO2.49, DISCO2A.50
GND: DISCO1.1, DISCO1A.2, MOSTEK_H.GND1 (GND), MOSTEK_H.GND2 (GND), MOSTEK_H.GND3 (GND), ZAS_LOG.2, ZAS_MOT.2
GNDA: DISCO1.49, DISCO1A.50
unnamed: JP5.1, JP5.2
unnamed: JP5.3, JP5.4
unnamed: JP5.5, JP5.6
unnamed: JP5.7, JP5.8
unnamed: JP5.9, JP5.10
unnamed: JP5.11, JP5.12
unnamed: JP5.13, JP5.14
unnamed: JP5.15, JP5.16
unnamed: JP6.1, JP6.2
unnamed: JP6.3, JP6.4
unnamed: JP6.5, JP6.6
unnamed: JP6.7, JP6.8
unnamed: JP6.9, JP6.10
unnamed: JP6.11, JP6.12
unnamed: JP6.13, JP6.14
unnamed: JP6.15, JP6.16
unnamed: C1.+, IC1.1 (VI), JP7.1
unnamed: C2.+, C3.1, IC1.3 (VO), JP8.1
unnamed: C1.-, C2.-, C3.2, IC1.2 (GND), JP7.2, JP8.2
unnamed: DISCO1.2, DISCO1A.1
unnamed: DISCO1.4, DISCO1A.3
unnamed: DISCO1.6, DISCO1A.5
unnamed: DISCO1.8, DISCO1A.7
unnamed: DISCO1.10, DISCO1A.9
unnamed: DISCO1.12, DISCO1A.11
unnamed: DISCO1.14, DISCO1A.13
unnamed: DISCO1.16, DISCO1A.15
unnamed: DISCO1.18, DISCO1A.17
unnamed: DISCO1.20, DISCO1A.19
unnamed: DISCO1.22, DISCO1A.21
unnamed: DISCO1.24, DISCO1A.23
unnamed: DISCO1.26, DISCO1A.25
unnamed: DISCO1.28, DISCO1A.27
unnamed: DISCO1.30, DISCO1A.29
unnamed: DISCO1.32, DISCO1A.31
unnamed: DISCO1.34, DISCO1A.33
unnamed: DISCO1.36, DISCO1A.35
unnamed: DISCO1.38, DISCO1A.37
unnamed: DISCO1.40, DISCO1A.39
unnamed: DISCO1.42, DISCO1A.41
unnamed: DISCO1.44, DISCO1A.43
unnamed: DISCO1.46, DISCO1A.45
unnamed: DISCO1.48, DISCO1A.47
unnamed: DISCO1.50, DISCO1A.49
unnamed: DISCO2.2, DISCO2A.1
unnamed: DISCO2.4, DISCO2A.3
unnamed: DISCO2.6, DISCO2A.5
unnamed: DISCO2.8, DISCO2A.7
unnamed: DISCO2.10, DISCO2A.9
unnamed: DISCO2.12, DISCO2A.11
unnamed: DISCO2.14, DISCO2A.13
unnamed: DISCO2.16, DISCO2A.15
unnamed: DISCO2.18, DISCO2A.17
unnamed: DISCO2.20, DISCO2A.19
unnamed: DISCO2.22, DISCO2A.21
unnamed: DISCO2.24, DISCO2A.23
unnamed: DISCO2.26, DISCO2A.25
unnamed: DISCO2.28, DISCO2A.27
unnamed: DISCO2.30, DISCO2A.29
unnamed: DISCO2.32, DISCO2A.31
unnamed: DISCO2.34, DISCO2A.33
unnamed: DISCO2.36, DISCO2A.35
unnamed: DISCO2.38, DISCO2A.37
unnamed: DISCO2.40, DISCO2A.39
unnamed: DISCO2.42, DISCO2A.41
unnamed: DISCO2.44, DISCO2A.43
unnamed: DISCO2.46, DISCO2A.45
unnamed: DISCO2.48, DISCO2A.47
unnamed: DISCO2.50, DISCO2A.49
unnamed: JP9.1, JP9.2
unnamed: JP9.3, JP9.4
unnamed: JP9.5, JP9.6
unnamed: JP9.7, JP9.8
unnamed: JP9.9, JP9.10
unnamed: JP9.11, JP9.12
unnamed: JP9.13, JP9.14
unnamed: JP9.15, JP9.16
unnamed: JP9.17, JP9.18
unnamed: JP9.19, JP9.20
unnamed: JP10.1, JP10.2
unnamed: JP10.3, JP10.4
unnamed: JP10.5, JP10.6
unnamed: JP10.7, JP10.8
unnamed: JP10.9, JP10.10
unnamed: JP10.11, JP10.12
unnamed: JP10.13, JP10.14
unnamed: JP10.15, JP10.16
unnamed: JP10.17, JP10.18
unnamed: JP10.19, JP10.20
NC: DISCO1.47, DISCO1A.48
NRST: DISCO1.5, DISCO1A.6
PA0: DISCO1.11, DISCO1A.12
PA2: DISCO1.13, DISCO1A.14
PA4: DISCO1.15, DISCO1A.16
PA6: DISCO1.17, DISCO1A.18
PB0: DISCO1.21, DISCO1A.22
PB2: DISCO1.23, DISCO1A.24
PB10: DISCO1.33, DISCO1A.34
PB12: DISCO1.35, DISCO1A.36
PB14: DISCO1.37, DISCO1A.38
PC0: DISCO1.7, DISCO1A.8
PC2: DISCO1.9, DISCO1A.10
PC4: DISCO1.19, DISCO1A.20
PD8: DISCO1.39, DISCO1A.40
PD10: DISCO1.41, DISCO1A.42
PD12: DISCO1.43, DISCO1A.44
PD14: DISCO1.45, DISCO1A.46
PE8: DISCO1.25, DISCO1A.26
PE10: DISCO1.27, DISCO1A.28
PE12: DISCO1.29, DISCO1A.30
PE14: DISCO1.31, DISCO1A.32
VCC: MOSTEK_H.VCC
VDD: DISCO1.3, DISCO1A.4
VMOT: MOSTEK_H.VMOT, ZAS_MOT.1

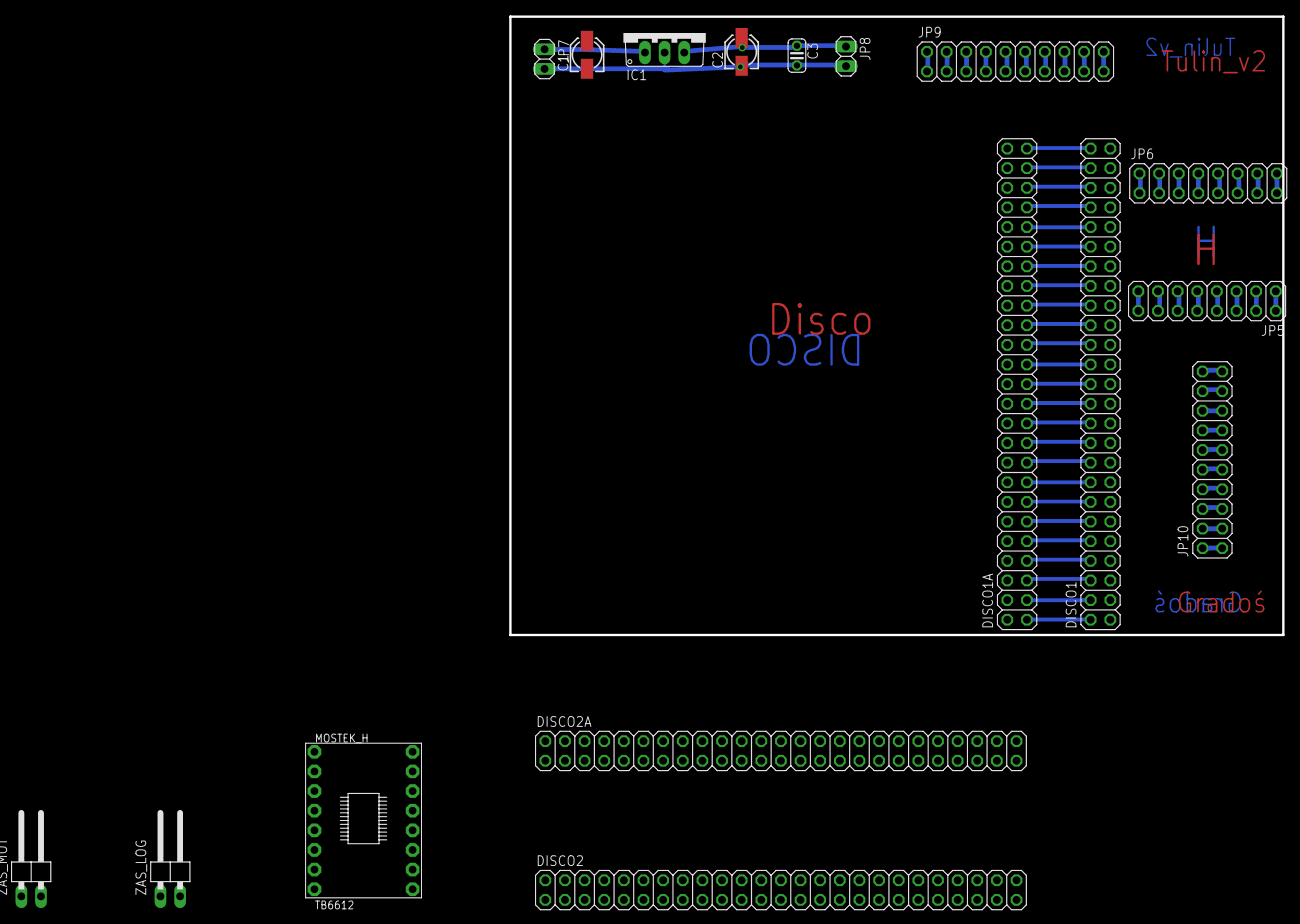
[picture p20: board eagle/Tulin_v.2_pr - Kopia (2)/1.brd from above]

Board: 2 copper layers, 100.0 x 80.0 mm, 17 parts (0 on the bottom side), 140 nets.

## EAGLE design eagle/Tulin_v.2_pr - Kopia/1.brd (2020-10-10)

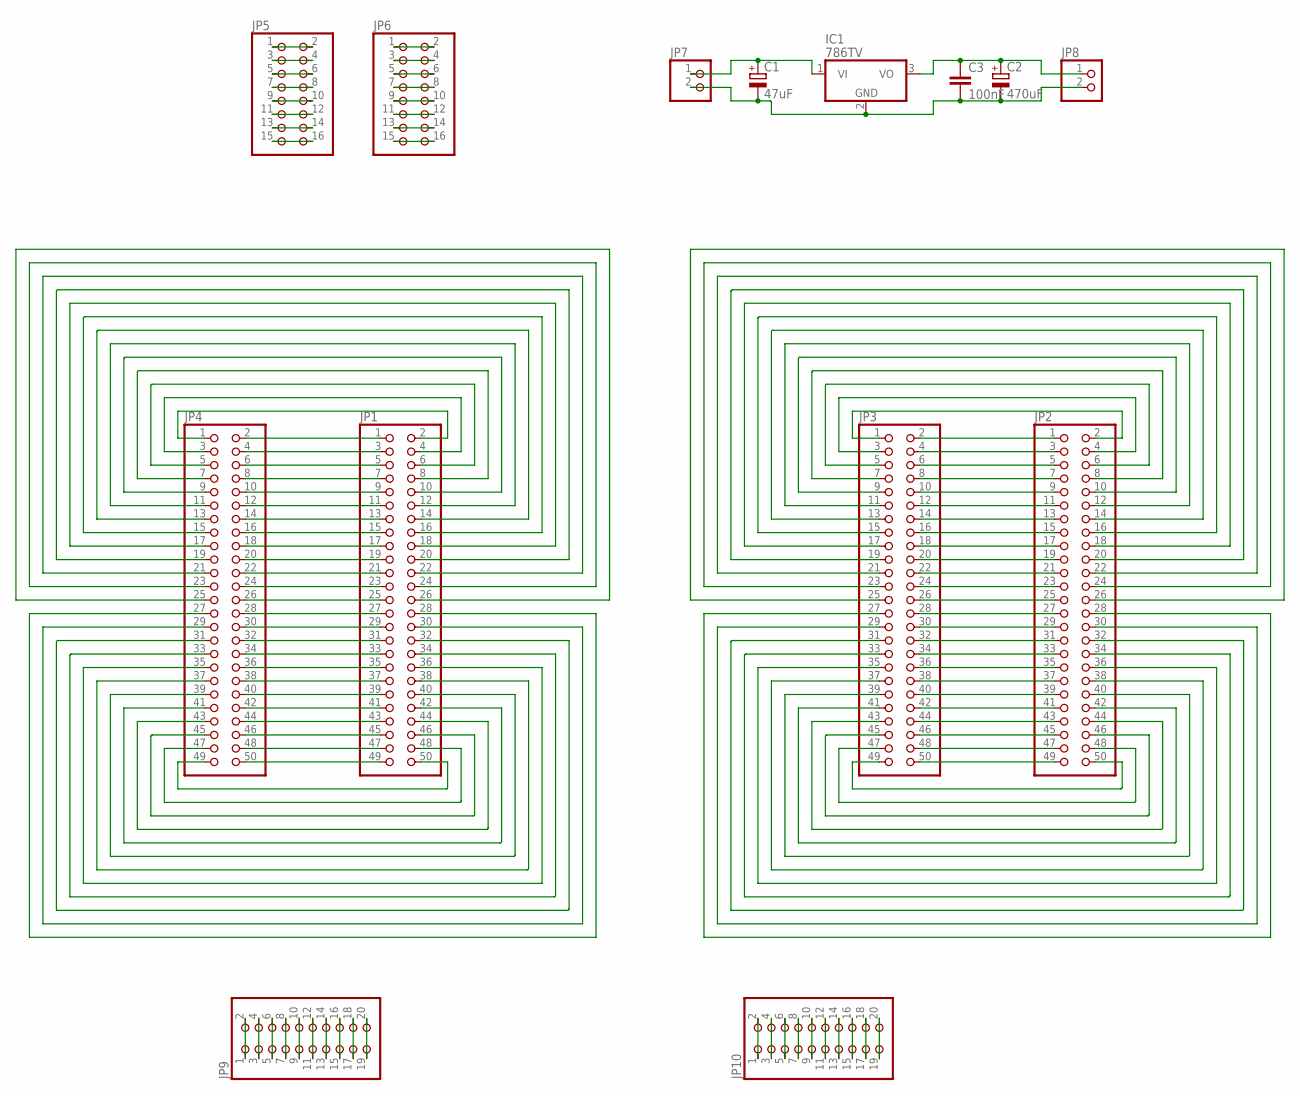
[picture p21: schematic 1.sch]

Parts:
C1: 47uF; 153CLV-0405
C2: 470uF; 153CLV-0405
C3: 100nF; C025-024X044
IC1: 786TV; TO220V
JP1, JP2, JP3, JP4: PINHD-2X25; 2X25
JP5, JP6: PINHD-2X8; 2X08
JP7, JP8: PINHD-1X2; 1X02
JP9, JP10: PINHD-2X10; 2X10

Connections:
unnamed: JP5.1, JP5.2
unnamed: JP5.3, JP5.4
unnamed: JP5.5, JP5.6
unnamed: JP5.7, JP5.8
unnamed: JP5.9, JP5.10
unnamed: JP5.11, JP5.12
unnamed: JP5.13, JP5.14
unnamed: JP5.15, JP5.16
unnamed: JP6.1, JP6.2
unnamed: JP6.3, JP6.4
unnamed: JP6.5, JP6.6
unnamed: JP6.7, JP6.8
unnamed: JP6.9, JP6.10
unnamed: JP6.11, JP6.12
unnamed: JP6.13, JP6.14
unnamed: JP6.15, JP6.16
unnamed: C1.+, IC1.1 (VI), JP7.1
unnamed: C2.+, C3.1, IC1.3 (VO), JP8.1
unnamed: C1.-, C2.-, C3.2, IC1.2 (GND), JP7.2, JP8.2
unnamed: JP1.2, JP4.1
unnamed: JP1.1, JP4.2
unnamed: JP1.3, JP4.4
unnamed: JP1.5, JP4.6
unnamed: JP1.7, JP4.8
unnamed: JP1.9, JP4.10
unnamed: JP1.11, JP4.12
unnamed: JP1.13, JP4.14
unnamed: JP1.15, JP4.16
unnamed: JP1.17, JP4.18
unnamed: JP1.19, JP4.20
unnamed: JP1.21, JP4.22
unnamed: JP1.23, JP4.24
unnamed: JP1.25, JP4.26
unnamed: JP1.27, JP4.28
unnamed: JP1.29, JP4.30
unnamed: JP1.31, JP4.32
unnamed: JP1.33, JP4.34
unnamed: JP1.35, JP4.36
unnamed: JP1.37, JP4.38
unnamed: JP1.39, JP4.40
unnamed: JP1.41, JP4.42
unnamed: JP1.43, JP4.44
unnamed: JP1.45, JP4.46
unnamed: JP1.47, JP4.48
unnamed: JP1.4, JP4.3
unnamed: JP1.6, JP4.5
unnamed: JP1.8, JP4.7
unnamed: JP1.10, JP4.9
unnamed: JP1.12, JP4.11
unnamed: JP1.14, JP4.13
unnamed: JP1.16, JP4.15
unnamed: JP1.18, JP4.17
unnamed: JP1.20, JP4.19
unnamed: JP1.22, JP4.21
unnamed: JP1.24, JP4.23
unnamed: JP1.26, JP4.25
unnamed: JP1.50, JP4.49
unnamed: JP1.48, JP4.47
unnamed: JP1.46, JP4.45
unnamed: JP1.44, JP4.43
unnamed: JP1.42, JP4.41
unnamed: JP1.40, JP4.39
unnamed: JP1.38, JP4.37
unnamed: JP1.36, JP4.35
unnamed: JP1.34, JP4.33
unnamed: JP1.32, JP4.31
unnamed: JP1.30, JP4.29
unnamed: JP1.28, JP4.27
unnamed: JP1.49, JP4.50
unnamed: JP2.1, JP3.2
unnamed: JP2.3, JP3.4
unnamed: JP2.5, JP3.6
unnamed: JP2.7, JP3.8
unnamed: JP2.9, JP3.10
unnamed: JP2.11, JP3.12
unnamed: JP2.13, JP3.14
unnamed: JP2.15, JP3.16
unnamed: JP2.17, JP3.18
unnamed: JP2.19, JP3.20
unnamed: JP2.21, JP3.22
unnamed: JP2.23, JP3.24
unnamed: JP2.25, JP3.26
unnamed: JP2.27, JP3.28
unnamed: JP2.29, JP3.30
unnamed: JP2.31, JP3.32
unnamed: JP2.33, JP3.34
unnamed: JP2.35, JP3.36
unnamed: JP2.37, JP3.38
unnamed: JP2.39, JP3.40
unnamed: JP2.41, JP3.42
unnamed: JP2.43, JP3.44
unnamed: JP2.45, JP3.46
unnamed: JP2.47, JP3.48
unnamed: JP2.2, JP3.1
unnamed: JP2.4, JP3.3
unnamed: JP2.6, JP3.5
unnamed: JP2.8, JP3.7
unnamed: JP2.10, JP3.9
unnamed: JP2.12, JP3.11
unnamed: JP2.14, JP3.13
unnamed: JP2.16, JP3.15
unnamed: JP2.18, JP3.17
unnamed: JP2.20, JP3.19
unnamed: JP2.22, JP3.21
unnamed: JP2.24, JP3.23
unnamed: JP2.26, JP3.25
unnamed: JP2.50, JP3.49
unnamed: JP2.48, JP3.47
unnamed: JP2.46, JP3.45
unnamed: JP2.44, JP3.43
unnamed: JP2.42, JP3.41
unnamed: JP2.40, JP3.39
unnamed: JP2.38, JP3.37
unnamed: JP2.36, JP3.35
unnamed: JP2.34, JP3.33
unnamed: JP2.32, JP3.31
unnamed: JP2.30, JP3.29
unnamed: JP2.28, JP3.27
unnamed: JP2.49, JP3.50
unnamed: JP9.1, JP9.2
unnamed: JP9.3, JP9.4
unnamed: JP9.5, JP9.6
unnamed: JP9.7, JP9.8
unnamed: JP9.9, JP9.10
unnamed: JP9.11, JP9.12
unnamed: JP9.13, JP9.14
unnamed: JP9.15, JP9.16
unnamed: JP9.17, JP9.18
unnamed: JP9.19, JP9.20
unnamed: JP10.1, JP10.2
unnamed: JP10.3, JP10.4
unnamed: JP10.5, JP10.6
unnamed: JP10.7, JP10.8
unnamed: JP10.9, JP10.10
unnamed: JP10.11, JP10.12
unnamed: JP10.13, JP10.14
unnamed: JP10.15, JP10.16
unnamed: JP10.17, JP10.18
unnamed: JP10.19, JP10.20

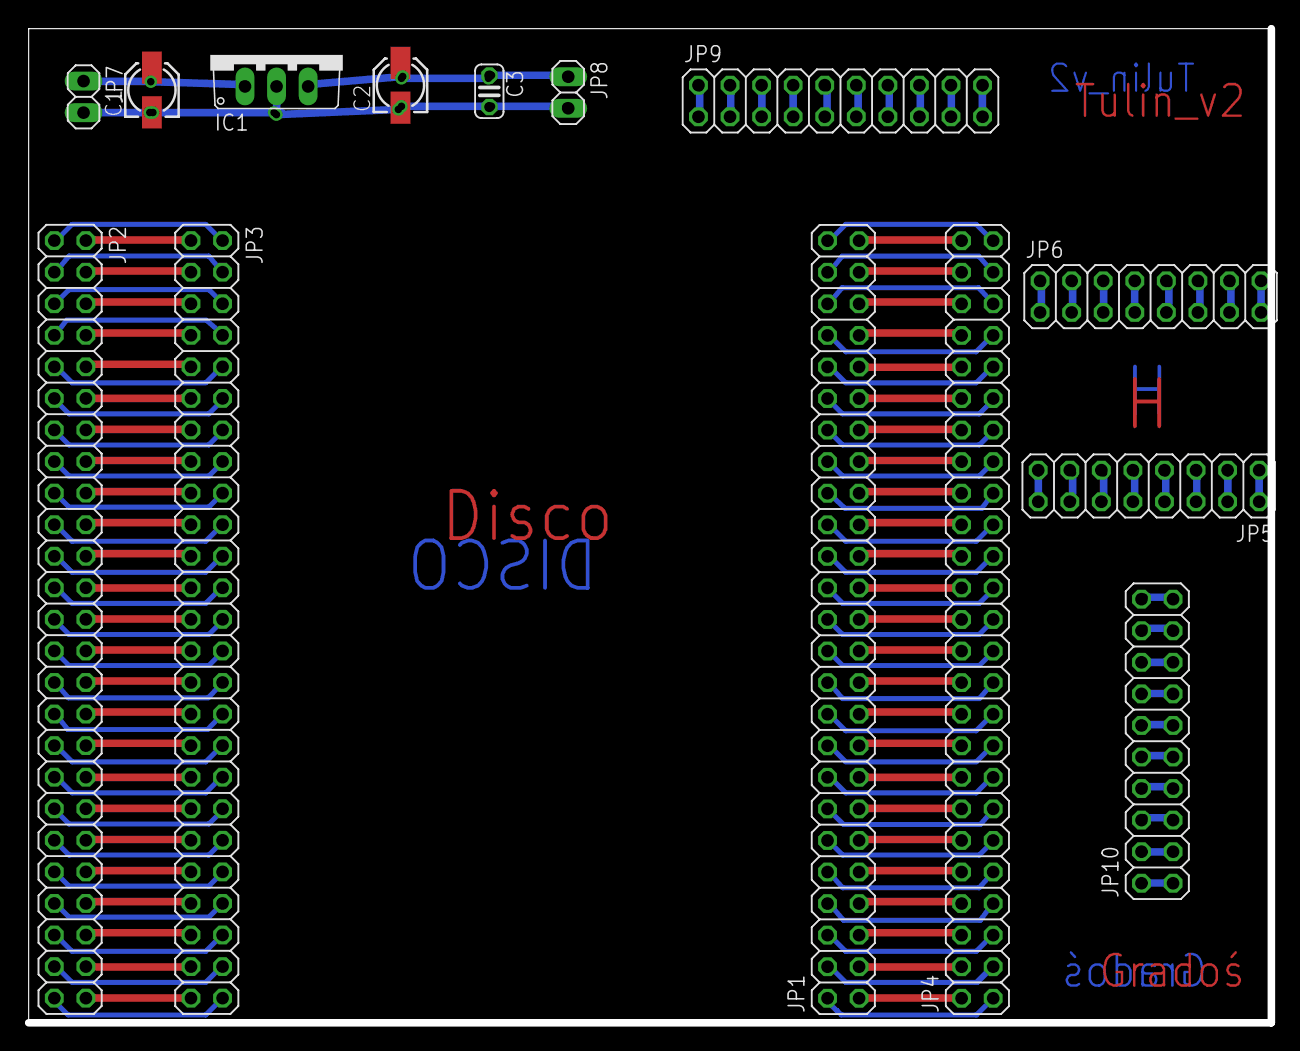
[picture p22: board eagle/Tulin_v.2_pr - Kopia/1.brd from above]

Board: 2 copper layers, 100.0 x 80.0 mm, 14 parts (0 on the bottom side), 139 nets.

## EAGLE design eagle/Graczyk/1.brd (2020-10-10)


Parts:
C1, C2, C3, C5, C6: 100n; C050-025X075
C4: 22u; B45181A
C7, C8, C9, C11, C12: C-EU050-025X075; C050-025X075
C10: CPOL-EUB45181A; B45181A
L1, L3, L4: L-US0207/10; 0207/10
L2: 10u; 0207/10
LED1, LED2: LEDIRL80A; IRL80A
R1: 10K; 0204/5
R2, R3, R4: R-EU_0204/5; 0204/5
S3: SD4-06
U1: ATMEGA328P_PDIP_EZ; DIP28-SIMON-KIT
U3: ATMEGA328P_TQFP; TQFP32-08
XTAL, XTAL1: 8MHz; Q

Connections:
GND3: C1.2, C2.2, C3.2, C4.-, C5.2, C6.2, C7.2, C8.2, C9.2, C10.-, C11.2, C12.2, U1.8 (GND), U1.22 (GND), U3.3 (GND), U3.5 (GND), U3.21 (AGND)
GPS-RX: U3.24 (PC1(ADC1))
GPS-TX: U3.23 (PC0(ADC0))
JOYSTICK_1_K_1: U1.23 (PC0(ADC0))
JOYSTICK_1_K_2: U1.24 (PC1(ADC1))
JOYSTICK_2_K_1: U1.25 (PC2(ADC2))
JOYSTICK_2_K_2: U1.26 (PC3(ADC3))
unnamed: R1.2, U1.1 (PC6(/RESET))
unnamed: C1.1, L1.2, L2.2, U1.20 (AVCC)
unnamed: C2.1, U1.21 (AREF)
unnamed: R2.2, U3.29 (PC6(/RESET))
unnamed: C6.1, U1.10 (PB7(XTAL2/TOSC2)), XTAL.2
unnamed: C5.1, U1.9 (PB6(XTAL1/TOSC1)), XTAL.1
unnamed: C7.1, L3.2, L4.2, U3.18 (AVCC)
unnamed: C8.1, U3.20 (AREF)
unnamed: C12.1, U3.8 (PB7(XTAL2/TOSC2)), XTAL1.2
unnamed: C11.1, U3.7 (PB6(XTAL1/TOSC1)), XTAL1.1
unnamed: LED1.K (C), R3.2
unnamed: S3.7, U1.14 (PB0(ICP))
unnamed: S3.8, U1.15 (PB1(OC1A))
unnamed: S3.9, U1.16 (PB2(SS/OC1B))
unnamed: S3.10, U1.17 (PB3(MOSI/OC2))
unnamed: S3.11, U1.18 (PB4(MISO))
unnamed: S3.12, U1.19 (PB5(SCK))
unnamed: LED2.K (C), R4.2
unnamed: R4.1, U1.13 (PD7(AIN1))
unnamed: R3.1, U1.11 (PD5(T1))
PRZYSPIESZENIOMIERZ_MAGNETOMETR_SCL: U3.28 (PC5(ADC5/SCL))
PRZYSPIESZENIOMIERZ_MAGNETOMETR_SDA: U3.27 (PC4(ADC4/SDA))
STEROWNIK_SILNIKA_1: U3.2 (PD4(XCK/T0))
STEROWNIK_SILNIKA_2: U3.9 (PD5(T1))
STEROWNIK_SILNIKA_3: U3.10 (PD6(AIN0))
STEROWNIK_SILNIKA_4: U3.11 (PD7(AIN1))
VCC: C3.1, C4.+, C9.1, C10.+, L1.1, L2.1, L3.1, L4.1, LED1.A, LED2.A, R1.1, R2.1, S3.1, S3.2, S3.3, S3.4, S3.5, S3.6, U1.7 (VCC), U3.4 (VCC)
XBEE-RX: U3.31 (PD1(TXD))
XBEE-TX: U3.30 (PD0(RXD))
ŻYROSKOP_MISO: U3.16 (PB4(MISO))
ŻYROSKOP_MOSI: U3.15 (PB3(MOSI/OC2))
ŻYROSKOP_SCK: U3.17 (PB5(SCK))

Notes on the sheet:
MIKROKONTROLER CZĘŚCI NAZIEMNEJ
MIKROKONTROLER CZĘŚCI POKŁADOWEJ
FILTRACJA NAPIĘCIA


Board: 2 copper layers, 100.0 x 80.0 mm, 27 parts (0 on the bottom side), 22 nets.

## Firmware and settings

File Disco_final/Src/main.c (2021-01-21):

/**
  ******************************************************************************
  * File Name          : main.c
  * Description        : Main program body (Disco)
	* Author             : Gradowski Kamil
	* Project name       : Tulin 
  ******************************************************************************

  */
/* Includes ------------------------------------------------------------------*/
#include "main.h"
#include "stm32f4xx_hal.h"

ADC_HandleTypeDef hadc1;
DMA_HandleTypeDef hdma_adc1;

TIM_HandleTypeDef htim1;
TIM_HandleTypeDef htim2;
TIM_HandleTypeDef htim3;
TIM_HandleTypeDef htim10;
DMA_HandleTypeDef hdma_tim2_ch1;
DMA_HandleTypeDef hdma_tim3_ch1_trig;

UART_HandleTypeDef huart1;

/* USER CODE BEGIN PV */
uint32_t Duty = 0; //SKRET
uint32_t Duty2 = 83; // PREDKOSC
uint32_t serwo = 21; // SKRET
uint16_t czujniki[5];
uint16_t tablica[5];
uint32_t kalibracja[5] = {0,0,0,0,0};
uint16_t prog = 1900;
uint8_t status = 0 ;
uint16_t czas_kalibracji = 100;
volatile uint8_t petla = 0; 
int wagi[7] = {-20, -10, 0, 10, 20};
int blad=0, pop_blad =0 , Kp = 1 , Kd = 1; 
uint32_t ile = 0;
volatile int test;
//static uint16_t cnt = 0; // Licznik wyslanych wiadomosci
uint8_t Data[50]; // Tablica przechowujaca wysylana wiadomosc.
uint16_t size = 0; // Rozmiar wysylanej wiadomosci
uint8_t Received;
float kb =0.6;
uint8_t flaga_nucleo;
uint32_t cnt_f =0;
uint8_t poprawka = 0;
uint8_t wiad = 0;

/* USER CODE END PV */

void SystemClock_Config(void);
static void MX_GPIO_Init(void);
static void MX_DMA_Init(void);
static void MX_TIM3_Init(void);
static void MX_TIM1_Init(void);
static void MX_ADC1_Init(void);
static void MX_TIM2_Init(void);
static void MX_TIM10_Init(void);
static void MX_USART1_UART_Init(void);

void HAL_TIM_MspPostInit(TIM_HandleTypeDef *htim);
                                
                                

/* USER CODE BEGIN PFP */
void HAL_GPIO_EXTI_Callback(uint16_t GPIO_Pin){
 if(GPIO_Pin == Button_Pin){
	 status =!status;               // ON/OFF
	 	if(status == 1) Duty2 = 25;	  // predkosc poczatkowa - ON
		else Duty2 = 0;               // OFF
 }
 }
//Przerwanie 100Hz, do glownej petli programu
void HAL_TIM_PeriodElapsedCallback(TIM_HandleTypeDef *htim){
 if(htim->Instance == TIM10){	 
	 petla = 1;
	 cnt_f++;
 }
 }
 
// Przerwanie wywolywane z czestotliwoscia 1KHz
void HAL_SYSTICK_Callback(void)
	
	{
		

		
  }
	
	//FUNKCJA DO USTALANIA PROGU - KALIBRACJI CZUJNIKÓW
	void kalibracja_progu()
	{
		for(int j = 0 ; j < czas_kalibracji ; j++) 
		{
			for( int i = 0 ; i < 5 ; i++)
			{
			kalibracja[i] = kalibracja[i] + czujniki[i]; // Sumowanie wartosci z czujników linii
			}
			
		}
		for( int k = 0 ; k < 5 ; k++)
		{
			kalibracja[k]= (kalibracja[k] / czas_kalibracji) ; //usrednienie wartosci z czujników
		}
		
	}
	
	// FUNKCJA DETEKCJI LINII
	void czytaj_adc()
	{
		for( int i = 0 ; i < 5 ; i++)                // przeszukiwanie tablicy z wartosciami napiec
		{
			if(czujniki[i] > ( kalibracja[i] + prog) ) // zamiana wartosci napiec z transoptorow
			{                                          // na tablice zawierajaca informacje o wykryciu linii
				tablica[i] = 1;                          // wykrycie linii
			}
			else
			{
				tablica[i] = 0;                           // brak wykrycia linii
			}
				
		}
		
	}


	int licz_blad() 
{ 
    int err = 0;                         // wartosc bledu 
    int ilosc = 0;                        // ilosc czujników z wykryta linia 
    
    for(int i=0; i<5; i++) 
    { 
        err += tablica[i]*wagi[i];        // wymnozenie czujnikow przez wagi 
        ilosc += tablica[i];              // tablica[i] ma wartosc 1/0 wiec zliczamy 
    }                                     // czujniki pod którymi wykryto linie
    
    err = err / ilosc;                        // usrednienie wartosci bledu
    
    return err; 
}

int PD() 
{ 
    //wynik funkcji licz_blad() przechowywany jest w zmiennej blad
    int rozniczka = blad - pop_blad;   // obliczanie czlonu rozniczkujacego
    pop_blad = blad; 
    return Kp*blad + Kd*rozniczka;    // przypisanie wag do czlonow
}
/* Funkcja szukania linii po zgubieniu */
void szukanie_ln()
{
	uint8_t ilosc_cz = 0;
	uint8_t sz_blad = 0;
	uint8_t czas_zgubienia = 0;
	
	/* przeszukiwanie tablicy czujnikow */
	for(int l=0; l<5 ; l++)
	{
		ilosc_cz += tablica[l]; //zliczanie ilosci czujnikow pod ktorymi jest linia
	}
	/* jezeli wykryto linie i blad jest wiekszy od zera */
	if((ilosc_cz > 0) ^ (blad > 0)) 
	{
		sz_blad = blad;        // zachowanie wartosci bledu w zmiennej sz_blad
		czas_zgubienia = 0;
	}
	else                     // nie ma lini pod czujnikami
	{
		czas_zgubienia++;      // inkrementacja czasu braku lini pod czujnikami
		/* jezeli nie ma linii pod czujnikami i jezeli blad wynosi 0
		i jezeli trwa to od 0,5 s */
		if ((blad == 0) ^ (czas_zgubienia > 50))
		{
			blad = sz_blad;     // przypisanie do aktualnego bledu ostatnia porawna wartosc
		}
	}
}
/* Funkcja awaryjnego lub zdalnego zatrzymania robota */
void stop()
{
	if(flaga_nucleo == 6)     // jesli otrzymano polecenie STOP
	{
		status = 0;             // zatrzymaj silnik
	}
	else if( cnt_f == 2000)   //jesli przez 20s nie otrzymano zadnego polecenia
	{
		if(flaga_nucleo == 0)
		{
			status = 0;          // zatrzymaj silnik
		}
		flaga_nucleo = 0;      // wyzerowanie flagi wiadomosci
		cnt_f = 0;             // wyzerowanie licznika czasu
	}
	
}
//  UART

// UART!!!!!!!!!! - Bluetooth
void HAL_UART_RxCpltCallback(UART_HandleTypeDef *huart) {
 
 uint8_t Data[50]; // Tablica przechowujaca wysylana wiadomosc.
 uint16_t size = 0; // Rozmiar wysylanej wiadomosci
 
 // Odebrany znak zostaje przekonwertowany na liczbe calkowita i sprawdzony
 // instrukcja warunkowa 
	
 switch (atoi((char*)&Received)) {
 
 case 2: // Jezeli odebrany zostanie znak 2
 wiad = 1;
 HAL_GPIO_WritePin(GPIOD, GPIO_PIN_13, GPIO_PIN_SET);
 flaga_nucleo = 2;
 
 break;
 
 case 8: // Jezeli odebrany zostanie znak 8
wiad = 1;
 HAL_GPIO_WritePin(GPIOD, GPIO_PIN_13, GPIO_PIN_RESET);
 flaga_nucleo = 8;
 
 break;
 
 case 6: // Jezeli odebrany zostanie znak 6
wiad = 1;
 flaga_nucleo = 6;
 
 
 break;
 
 case 3: // Jezeli odebrany zostanie znak 3
wiad = 1;
 flaga_nucleo = 3;
 
 
 //default: // Jezeli odebrano nieobslugiwany znak
 //size = sprintf(Data, "Odebrano nieznany znak: %c\n\r", Received[10]);
 
 }
 HAL_UART_Transmit_IT(&huart1, Data, size); // Rozpoczecie nadawania danych z wykorzystaniem przerwan
 HAL_UART_Receive_IT(&huart1, &Received, 1); // Ponowne wlaczenie nasluchiwania
 }

/* USER CODE END PFP */

int main(void)
{

  /* MCU Configuration----------------------------------------------------------*/

  /* Reset of all peripherals, Initializes the Flash interface and the Systick. */
  HAL_Init();

  /* Configure the system clock */
  SystemClock_Config();

  /* Initialize all configured peripherals */
  MX_GPIO_Init();
  MX_DMA_Init();
  MX_TIM3_Init();
  MX_TIM1_Init();
  MX_ADC1_Init();
  MX_TIM2_Init();
  MX_TIM10_Init();
  MX_USART1_UART_Init();

  /* USER CODE BEGIN 2 */
HAL_TIM_PWM_Start_DMA(&htim3, TIM_CHANNEL_1, &Duty, 1);
HAL_TIM_PWM_Start_DMA(&htim2, TIM_CHANNEL_1, &Duty2, 1);
HAL_TIM_Encoder_Start(&htim1, TIM_CHANNEL_ALL);
HAL_ADC_Start_IT(&hadc1);
HAL_ADC_Start_DMA(&hadc1, (uint32_t*)czujniki, 5);
HAL_GPIO_WritePin(GPIOD, GPIO_PIN_1, GPIO_PIN_RESET);
HAL_GPIO_WritePin(GPIOD, GPIO_PIN_2, GPIO_PIN_SET);
HAL_TIM_Base_Start_IT(&htim10);
HAL_UART_Receive_IT(&huart1, &Received, 1);

kalibracja_progu();
  /* USER CODE END 2 */

  /* Infinite loop */
  /* USER CODE BEGIN WHILE */
  while (1)
  {
  /* USER CODE END WHILE */

  /* USER CODE BEGIN 3 */
szukanie_ln();
Duty = serwo;                                    		// sterowanie kolami
if( Duty >= 50) Duty = 50;													 // ograniczenie ruchow serwa
if (Duty <=0) Duty = 0;		
		
		// JAZDA. STATUS I PREDKOSC
	if(wiad == 1)
	{
	if(flaga_nucleo == 2 ) Duty2 = Duty2 + 5;         //przyspiesz
	else if(flaga_nucleo == 8) Duty2 = Duty2 - 5;	    //zwolnij
		wiad = 0;
	}
   	
		if(petla)
		{
			HAL_GPIO_TogglePin(GPIOD, GPIO_PIN_14);
			
		  czytaj_adc();
			
			blad = licz_blad();
			
			poprawka = PD();  // regulator PD
// nanoszenie poprawki - reakcja na blad
				serwo = 21 + (kb*poprawka);
				if( serwo >= 50) serwo = 50;
				if (serwo <=0) serwo = 0;	
			
			petla = 0;
		}
		
  /* USER CODE END 3 */

}
	}

/** System Clock Configuration
*/
void SystemClock_Config(void)
{

  RCC_OscInitTypeDef RCC_OscInitStruct;
  RCC_ClkInitTypeDef RCC_ClkInitStruct;

    /**Configure the main internal regulator output voltage 
    */
  __HAL_RCC_PWR_CLK_ENABLE();

  __HAL_PWR_VOLTAGESCALING_CONFIG(PWR_REGULATOR_VOLTAGE_SCALE1);

    /**Initializes the CPU, AHB and APB busses clocks 
    */
  RCC_OscInitStruct.OscillatorType = RCC_OSCILLATORTYPE_HSE;
  RCC_OscInitStruct.HSEState = RCC_HSE_ON;
  RCC_OscInitStruct.PLL.PLLState = RCC_PLL_ON;
  RCC_OscInitStruct.PLL.PLLSource = RCC_PLLSOURCE_HSE;
  RCC_OscInitStruct.PLL.PLLM = 4;
  RCC_OscInitStruct.PLL.PLLN = 100;
  RCC_OscInitStruct.PLL.PLLP = RCC_PLLP_DIV2;
  RCC_OscInitStruct.PLL.PLLQ = 8;
  if (HAL_RCC_OscConfig(&RCC_OscInitStruct) != HAL_OK)
  {
    _Error_Handler(__FILE__, __LINE__);
  }

    /**Initializes the CPU, AHB and APB busses clocks 
    */
  RCC_ClkInitStruct.ClockType = RCC_CLOCKTYPE_HCLK|RCC_CLOCKTYPE_SYSCLK
                              |RCC_CLOCKTYPE_PCLK1|RCC_CLOCKTYPE_PCLK2;
  RCC_ClkInitStruct.SYSCLKSource = RCC_SYSCLKSOURCE_PLLCLK;
  RCC_ClkInitStruct.AHBCLKDivider = RCC_SYSCLK_DIV1;
  RCC_ClkInitStruct.APB1CLKDivider = RCC_HCLK_DIV2;
  RCC_ClkInitStruct.APB2CLKDivider = RCC_HCLK_DIV1;

  if (HAL_RCC_ClockConfig(&RCC_ClkInitStruct, FLASH_LATENCY_3) != HAL_OK)
  {
    _Error_Handler(__FILE__, __LINE__);
  }

    /**Configure the Systick interrupt time 
    */
  HAL_SYSTICK_Config(HAL_RCC_GetHCLKFreq()/1000);

    /**Configure the Systick 
    */
  HAL_SYSTICK_CLKSourceConfig(SYSTICK_CLKSOURCE_HCLK);

  /* SysTick_IRQn interrupt configuration */
  HAL_NVIC_SetPriority(SysTick_IRQn, 0, 0);
}

/* ADC1 init function */
static void MX_ADC1_Init(void)
{

  ADC_ChannelConfTypeDef sConfig;

    /**Configure the global features of the ADC (Clock, Resolution, Data Alignment and number of conversion) 
    */
  hadc1.Instance = ADC1;
  hadc1.Init.ClockPrescaler = ADC_CLOCK_SYNC_PCLK_DIV8;
  hadc1.Init.Resolution = ADC_RESOLUTION_12B;
  hadc1.Init.ScanConvMode = ENABLE;
  hadc1.Init.ContinuousConvMode = ENABLE;
  hadc1.Init.DiscontinuousConvMode = DISABLE;
  hadc1.Init.ExternalTrigConvEdge = ADC_EXTERNALTRIGCONVEDGE_NONE;
  hadc1.Init.ExternalTrigConv = ADC_SOFTWARE_START;
  hadc1.Init.DataAlign = ADC_DATAALIGN_RIGHT;
  hadc1.Init.NbrOfConversion = 5;
  hadc1.Init.DMAContinuousRequests = ENABLE;
  hadc1.Init.EOCSelection = ADC_EOC_SINGLE_CONV;
  if (HAL_ADC_Init(&hadc1) != HAL_OK)
  {
    _Error_Handler(__FILE__, __LINE__);
  }

    /**Configure for the selected ADC regular channel its corresponding rank in the sequencer and its sample time. 
    */
  sConfig.Channel = ADC_CHANNEL_1;
  sConfig.Rank = 1;
  sConfig.SamplingTime = ADC_SAMPLETIME_480CYCLES;
  if (HAL_ADC_ConfigChannel(&hadc1, &sConfig) != HAL_OK)
  {
    _Error_Handler(__FILE__, __LINE__);
  }

    /**Configure for the selected ADC regular channel its corresponding rank in the sequencer and its sample time. 
    */
  sConfig.Channel = ADC_CHANNEL_2;
  sConfig.Rank = 2;
  if (HAL_ADC_ConfigChannel(&hadc1, &sConfig) != HAL_OK)
  {
    _Error_Handler(__FILE__, __LINE__);
  }

    /**Configure for the selected ADC regular channel its corresponding rank in the sequencer and its sample time. 
    */
  sConfig.Channel = ADC_CHANNEL_3;
  sConfig.Rank = 3;
  if (HAL_ADC_ConfigChannel(&hadc1, &sConfig) != HAL_OK)
  {
    _Error_Handler(__FILE__, __LINE__);
  }

    /**Configure for the selected ADC regular channel its corresponding rank in the sequencer and its sample time. 
    */
  sConfig.Channel = ADC_CHANNEL_8;
  sConfig.Rank = 4;
  if (HAL_ADC_ConfigChannel(&hadc1, &sConfig) != HAL_OK)
  {
    _Error_Handler(__FILE__, __LINE__);
  }

    /**Configure for the selected ADC regular channel its corresponding rank in the sequencer and its sample time. 
    */
  sConfig.Channel = ADC_CHANNEL_9;
  sConfig.Rank = 5;
  if (HAL_ADC_ConfigChannel(&hadc1, &sConfig) != HAL_OK)
  {
    _Error_Handler(__FILE__, __LINE__);
  }

}

/* TIM1 init function */
static void MX_TIM1_Init(void)
{

  TIM_Encoder_InitTypeDef sConfig;
  TIM_MasterConfigTypeDef sMasterConfig;

  htim1.Instance = TIM1;
  htim1.Init.Prescaler = 0;
  htim1.Init.CounterMode = TIM_COUNTERMODE_UP;
  htim1.Init.Period = 403;
  htim1.Init.ClockDivision = TIM_CLOCKDIVISION_DIV1;
  htim1.Init.RepetitionCounter = 0;
  sConfig.EncoderMode = TIM_ENCODERMODE_TI12;
  sConfig.IC1Polarity = TIM_ICPOLARITY_RISING;
  sConfig.IC1Selection = TIM_ICSELECTION_DIRECTTI;
  sConfig.IC1Prescaler = TIM_ICPSC_DIV1;
  sConfig.IC1Filter = 15;
  sConfig.IC2Polarity = TIM_ICPOLARITY_RISING;
  sConfig.IC2Selection = TIM_ICSELECTION_DIRECTTI;
  sConfig.IC2Prescaler = TIM_ICPSC_DIV1;
  sConfig.IC2Filter = 15;
  if (HAL_TIM_Encoder_Init(&htim1, &sConfig) != HAL_OK)
  {
    _Error_Handler(__FILE__, __LINE__);
  }

  sMasterConfig.MasterOutputTrigger = TIM_TRGO_RESET;
  sMasterConfig.MasterSlaveMode = TIM_MASTERSLAVEMODE_DISABLE;
  if (HAL_TIMEx_MasterConfigSynchronization(&htim1, &sMasterConfig) != HAL_OK)
  {
    _Error_Handler(__FILE__, __LINE__);
  }

}

/* TIM2 init function */
static void MX_TIM2_Init(void)
{

  TIM_ClockConfigTypeDef sClockSourceConfig;
  TIM_MasterConfigTypeDef sMasterConfig;
  TIM_OC_InitTypeDef sConfigOC;

  htim2.Instance = TIM2;
  htim2.Init.Prescaler = 19;
  htim2.Init.CounterMode = TIM_COUNTERMODE_UP;
  htim2.Init.Period = 99;
  htim2.Init.ClockDivision = TIM_CLOCKDIVISION_DIV1;
  if (HAL_TIM_Base_Init(&htim2) != HAL_OK)
  {
    _Error_Handler(__FILE__, __LINE__);
  }

  sClockSourceConfig.ClockSource = TIM_CLOCKSOURCE_INTERNAL;
  if (HAL_TIM_ConfigClockSource(&htim2, &sClockSourceConfig) != HAL_OK)
  {
    _Error_Handler(__FILE__, __LINE__);
  }

  if (HAL_TIM_PWM_Init(&htim2) != HAL_OK)
  {
    _Error_Handler(__FILE__, __LINE__);
  }

  sMasterConfig.MasterOutputTrigger = TIM_TRGO_RESET;
  sMasterConfig.MasterSlaveMode = TIM_MASTERSLAVEMODE_DISABLE;
  if (HAL_TIMEx_MasterConfigSynchronization(&htim2, &sMasterConfig) != HAL_OK)
  {
    _Error_Handler(__FILE__, __LINE__);
  }

  sConfigOC.OCMode = TIM_OCMODE_PWM1;
  sConfigOC.Pulse = 0;
  sConfigOC.OCPolarity = TIM_OCPOLARITY_HIGH;
  sConfigOC.OCFastMode = TIM_OCFAST_DISABLE;
  if (HAL_TIM_PWM_ConfigChannel(&htim2, &sConfigOC, TIM_CHANNEL_1) != HAL_OK)
  {
    _Error_Handler(__FILE__, __LINE__);
  }

  HAL_TIM_MspPostInit(&htim2);

}

/* TIM3 init function */
static void MX_TIM3_Init(void)
{

  TIM_ClockConfigTypeDef sClockSourceConfig;
  TIM_MasterConfigTypeDef sMasterConfig;
  TIM_OC_InitTypeDef sConfigOC;

  htim3.Instance = TIM3;
  htim3.Init.Prescaler = 4999;
  htim3.Init.CounterMode = TIM_COUNTERMODE_UP;
  htim3.Init.Period = 199;
  htim3.Init.ClockDivision = TIM_CLOCKDIVISION_DIV1;
  if (HAL_TIM_Base_Init(&htim3) != HAL_OK)
  {
    _Error_Handler(__FILE__, __LINE__);
  }

  sClockSourceConfig.ClockSource = TIM_CLOCKSOURCE_INTERNAL;
  if (HAL_TIM_ConfigClockSource(&htim3, &sClockSourceConfig) != HAL_OK)
  {
    _Error_Handler(__FILE__, __LINE__);
  }

  if (HAL_TIM_PWM_Init(&htim3) != HAL_OK)
  {
    _Error_Handler(__FILE__, __LINE__);
  }

  sMasterConfig.MasterOutputTrigger = TIM_TRGO_RESET;
  sMasterConfig.MasterSlaveMode = TIM_MASTERSLAVEMODE_DISABLE;
  if (HAL_TIMEx_MasterConfigSynchronization(&htim3, &sMasterConfig) != HAL_OK)
  {
    _Error_Handler(__FILE__, __LINE__);
  }

  sConfigOC.OCMode = TIM_OCMODE_PWM1;
  sConfigOC.Pulse = 0;
  sConfigOC.OCPolarity = TIM_OCPOLARITY_HIGH;
  sConfigOC.OCFastMode = TIM_OCFAST_DISABLE;
  if (HAL_TIM_PWM_ConfigChannel(&htim3, &sConfigOC, TIM_CHANNEL_1) != HAL_OK)
  {
    _Error_Handler(__FILE__, __LINE__);
  }

  HAL_TIM_MspPostInit(&htim3);

}

/* TIM10 init function */
static void MX_TIM10_Init(void)
{

  htim10.Instance = TIM10;
  htim10.Init.Prescaler = 99;
  htim10.Init.CounterMode = TIM_COUNTERMODE_UP;
  htim10.Init.Period = 9999;
  htim10.Init.ClockDivision = TIM_CLOCKDIVISION_DIV1;
  if (HAL_TIM_Base_Init(&htim10) != HAL_OK)
  {
    _Error_Handler(__FILE__, __LINE__);
  }

}

/* USART1 init function */
static void MX_USART1_UART_Init(void)
{

  huart1.Instance = USART1;
  huart1.Init.BaudRate = 9600;
  huart1.Init.WordLength = UART_WORDLENGTH_8B;
  huart1.Init.StopBits = UART_STOPBITS_1;
  huart1.Init.Parity = UART_PARITY_NONE;
  huart1.Init.Mode = UART_MODE_TX_RX;
  huart1.Init.HwFlowCtl = UART_HWCONTROL_NONE;
  huart1.Init.OverSampling = UART_OVERSAMPLING_16;
  if (HAL_UART_Init(&huart1) != HAL_OK)
  {
    _Error_Handler(__FILE__, __LINE__);
  }

}

/** 
  * Enable DMA controller clock
  */
static void MX_DMA_Init(void) 
{
  /* DMA controller clock enable */
  __HAL_RCC_DMA2_CLK_ENABLE();
  __HAL_RCC_DMA1_CLK_ENABLE();

  /* DMA interrupt init */
  /* DMA1_Stream4_IRQn interrupt configuration */
  HAL_NVIC_SetPriority(DMA1_Stream4_IRQn, 0, 0);
  HAL_NVIC_EnableIRQ(DMA1_Stream4_IRQn);
  /* DMA1_Stream5_IRQn interrupt configuration */
  HAL_NVIC_SetPriority(DMA1_Stream5_IRQn, 0, 0);
  HAL_NVIC_EnableIRQ(DMA1_Stream5_IRQn);
  /* DMA2_Stream0_IRQn interrupt configuration */
  HAL_NVIC_SetPriority(DMA2_Stream0_IRQn, 0, 0);
  HAL_NVIC_EnableIRQ(DMA2_Stream0_IRQn);

}
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

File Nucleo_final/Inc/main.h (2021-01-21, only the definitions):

#define B1_Pin GPIO_PIN_13
#define B1_GPIO_Port GPIOC
#define Button2_Pin GPIO_PIN_0
#define Button2_GPIO_Port GPIOC
#define Button2_EXTI_IRQn EXTI0_IRQn
#define Button1_Pin GPIO_PIN_2
#define Button1_GPIO_Port GPIOC
#define Button1_EXTI_IRQn EXTI2_IRQn
#define MOSI_Pin GPIO_PIN_3
#define MOSI_GPIO_Port GPIOC
#define USART_TX_Pin GPIO_PIN_2
#define USART_TX_GPIO_Port GPIOA
#define USART_RX_Pin GPIO_PIN_3
#define USART_RX_GPIO_Port GPIOA
#define PULSE_Pin GPIO_PIN_4
#define PULSE_GPIO_Port GPIOA
#define PULSE_EXTI_IRQn EXTI4_IRQn
#define LD2_Pin GPIO_PIN_5
#define LD2_GPIO_Port GPIOA
#define SCK_Pin GPIO_PIN_10
#define SCK_GPIO_Port GPIOB
#define CS_Pin GPIO_PIN_13
#define CS_GPIO_Port GPIOB
#define DC_Pin GPIO_PIN_14
#define DC_GPIO_Port GPIOB
#define RES_Pin GPIO_PIN_15
#define RES_GPIO_Port GPIOB
#define TMS_Pin GPIO_PIN_13
#define TMS_GPIO_Port GPIOA
#define TCK_Pin GPIO_PIN_14
#define TCK_GPIO_Port GPIOA
#define Button3_Pin GPIO_PIN_12
#define Button3_GPIO_Port GPIOC
#define SWO_Pin GPIO_PIN_3
#define SWO_GPIO_Port GPIOB

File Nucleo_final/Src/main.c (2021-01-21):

/**
*******************************************************************************
 * File Name          : main.c
  * Description        : Main program body (Nucleo)
	* Author             : Gradowski Kamil
	* Project name       : Tulin 
  ******************************************************************************
  */
/* Includes ------------------------------------------------------------------*/
#include "main.h"
#include "stm32f4xx_hal.h"
#include "SSD1331.h"

ADC_HandleTypeDef hadc1;
DMA_HandleTypeDef hdma_adc1;

SPI_HandleTypeDef hspi2;

TIM_HandleTypeDef htim10;

UART_HandleTypeDef huart1;
DMA_HandleTypeDef hdma_usart1_tx;
DMA_HandleTypeDef hdma_usart1_rx;

/* USER CODE BEGIN PV */
uint16_t Pulsometr;
int ile = 0;
uint32_t czas = 0;
uint8_t puls = 65;
uint8_t stary_puls = 65;
uint8_t zn_puls = 0;
volatile uint8_t k = 0, l = 0, flaga = 0, flaga2 = 0, tempo = 65;
//uint32_t cnt = 0; // Licznik 
uint8_t data[50]; // Tablica przechowujaca wysylana wiadomosc.
uint16_t size = 0; // Rozmiar wysylanej wiadomosci
uint8_t Received[1] = {0} ;
uint8_t sygnal = 0 , flaga_rs =0;

/* USER CODE END PV */

void SystemClock_Config(void);
static void MX_GPIO_Init(void);
static void MX_DMA_Init(void);
static void MX_ADC1_Init(void);
static void MX_TIM10_Init(void);
static void MX_SPI2_Init(void);
static void MX_USART1_UART_Init(void);

/* USER CODE BEGIN PFP */
void HAL_GPIO_EXTI_Callback(uint16_t GPIO_Pin){  //wywolanie funkcji przerwan zewnetrznych
	/*       Funkcja zliczania impulsow pulsomierza
	zmienna ile przechowuje informacje o ilosci impulsow z pulsomierza*/
	if(GPIO_Pin == PULSE_Pin){              //jezeli przerwanie pochodzi od pinu pulsomierza
	ile = ile + 1;                          // inkrementacja zmiennej  
	if(ile>=30) ile = 0 ;
	}
	
	if(GPIO_Pin == Button1_Pin)
	{
		//if(HAL_GPIO_ReadPin(Button1_GPIO_Port, Button1_Pin) == GPIO_PIN_RESET)	
		//	k++;
		flaga = 1;
	
	}
	if(GPIO_Pin == Button2_Pin)
	{
		l=1;
	}
	
}
/*Przerwanie pochodzace od timera wywolywane po uplynieciu wczesniej okreslonego czasu */
void HAL_TIM_PeriodElapsedCallback(TIM_HandleTypeDef *htim){ 
 if(htim->Instance == TIM10){ // Jezeli przerwanie pochodzi od timera 10
	 czas = czas + 1; // inkrementacja zmiennej sluzacej do obliczania czasu 
	 
	 if(czas >= 10000)      // Wywolywane co 10s
	 {
		/* Zmienna puls przechowuje informacje o bierzacym pulsie
		 Zmienna zn_puls przechowuje wartosc pulsu bedacego srednia wazona
		 obecnego pulsu i wczesniejszego */
		 puls= ile*6;                            // zlicza przez 10s, wiec trzeba pomnozyc przez 6
		 zn_puls = (((stary_puls) + (2*puls) )/3); // usrednienei pulsu z wart poprzenia
		 stary_puls = puls;                      //przypisanie obecnego pulsu jako wczesniejszego
		 ile = 0;                                //wyzerowanie ilosci impulsow
		 czas=0;                                 //wyzerowanie czasu
		 
		 /* decydowanie o tempie */
			if(zn_puls < (tempo - 5)) sygnal = 2 ;         // dyczyja o wyslaniu polecenia przyspiesz
				else if (zn_puls > (tempo + 5)) sygnal = 8;  // dyczyja o wyslaniu polecenia zwolnij
				else sygnal = 3;                             // decyzja o nie zmienianiu tempa
		 
		 /* flaga nakazujaca nadanie wiadomosci */ 
		 flaga_rs = 1; 
		
	 } 
 }
}
 // UART //
void HAL_UART_RxCpltCallback(UART_HandleTypeDef *huart) {
 
 static uint8_t Data[1]; // Tablica przechowujaca wysylana wiadomosc.
 
 //sprintf(Data, "Odebrana wiadomosc: %s\n\r", Received);
Data[0] = sygnal;
if(flaga_rs == 1)
{
 HAL_UART_Transmit_DMA(&huart1, Data, 1); // Rozpoczecie nadawania danych z wykorzystaniem przerwan
	flaga_rs = 0;
}
 HAL_UART_Receive_DMA(&huart1, Received, 1); // Ponowne wlaczenie nasluchiwania
// HAL_GPIO_TogglePin(LED_BLUE_GPIO_Port, LED_BLUE_Pin);
}

void liczenie_pulsu()
{
	
}

void menu1(uint8_t klik)
{

	//while(l==0)
	{
	switch(klik){
		case 0:
		ssd1331_display_string(0, 0, "    MENU  ", FONT_1608, GREEN);
		ssd1331_draw_line(2, 18, 92, 18, YELLOW);
		ssd1331_display_string(2, 20, " Wybierz puls:", FONT_1206, WHITE);
		ssd1331_display_string(2, 34, "- 100 [1/s]", FONT_1206, GREY);
		tempo = 100;
	
	break;
		
		case 1:
		ssd1331_display_string(0, 0, "    MENU  ", FONT_1608, GREEN);
		ssd1331_draw_line(2, 18, 92, 18, YELLOW);
		ssd1331_display_string(2, 20, " Wybierz puls:", FONT_1206, WHITE);
		ssd1331_display_string(2, 34, "- 110 [1/s]", FONT_1206, GREY);	
		tempo = 110;		
		break;
		
		case 2:
		ssd1331_display_string(0, 0, "    MENU  ", FONT_1608, GREEN);
		ssd1331_draw_line(2, 18, 92, 18, YELLOW);
		ssd1331_display_string(2, 20, " Wybierz puls:", FONT_1206, WHITE);
		ssd1331_display_string(2, 34, "- 120 [1/s]", FONT_1206, GREY);	
		tempo = 120;
		break;
		
		case 3:
		ssd1331_display_string(0, 0, "    MENU  ", FONT_1608, GREEN);
		ssd1331_draw_line(2, 18, 92, 18, YELLOW);
		ssd1331_display_string(2, 20, " Wybierz puls:", FONT_1206, WHITE);
		ssd1331_display_string(2, 34, "- 130 [1/s]", FONT_1206, GREY);	
		tempo = 130;
		break;
		
	}
	
}
}

void menu2(uint8_t klik)
{
	
}
/* USER CODE END PFP */

int main(void)
{

  /* MCU Configuration----------------------------------------------------------*/

  /* Reset of all peripherals, Initializes the Flash interface and the Systick. */
  HAL_Init();

  /* Configure the system clock */
  SystemClock_Config();

  /* Initialize all configured peripherals */
  MX_GPIO_Init();
  MX_DMA_Init();
  MX_ADC1_Init();
  MX_TIM10_Init();
  MX_SPI2_Init();
  MX_USART1_UART_Init();

  /* USER CODE BEGIN 2 */
HAL_ADC_Start_DMA(&hadc1, (uint32_t*)Pulsometr, 1);
HAL_TIM_Base_Start_IT(&htim10);

//HAL_UART_Transmit_IT(&huart1, data, size); // Rozpoczecie nadawania danych z wykorzystaniem przerwan

ssd1331_init();
ssd1331_clear_screen(BLACK);
ssd1331_display_string(0, 10, " Tulin_v.2 ", FONT_1608, RED);
ssd1331_display_string(0, 50, " GRADOWSKI Kamil", FONT_1206 , YELLOW);

HAL_Delay(1000);
ssd1331_clear_screen(BLACK);
ssd1331_display_string(0, 0, "    MENU  ", FONT_1608, GREEN);
ssd1331_draw_line(2, 18, 92, 18, YELLOW);
ssd1331_display_string(2, 20, " Wybierz puls:", FONT_1206, WHITE);



  /* USER CODE END 2 */

  /* Infinite loop */
  /* USER CODE BEGIN WHILE */
  while (1)
  {
  /* USER CODE END WHILE */

  /* USER CODE END WHILE */
		while(l==0)
		{
	while(flaga ==1)
	{
		while(HAL_GPIO_ReadPin(Button1_GPIO_Port, Button1_Pin) == GPIO_PIN_SET)	
		{
			ssd1331_clear_screen(BLACK);
			k++;
			if(k>=4) k=0;
			flaga =0;
			break;
			
		}
	}
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

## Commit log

2020-10-10 wersja (nie) finalna pracy
    [1.brd, 1.sch, 1_TRYY.brd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]
2021-01-21 pcb projects
    [1nuc_sluyba.brd, 1nuc_sluyba.sch]

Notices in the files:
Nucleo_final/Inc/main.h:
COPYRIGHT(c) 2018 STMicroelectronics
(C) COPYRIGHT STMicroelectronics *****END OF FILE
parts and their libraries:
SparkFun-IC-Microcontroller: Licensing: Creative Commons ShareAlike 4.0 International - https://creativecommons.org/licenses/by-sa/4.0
